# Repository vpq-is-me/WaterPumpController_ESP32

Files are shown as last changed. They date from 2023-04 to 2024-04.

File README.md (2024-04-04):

# Water pump controller.

This controller intended for control submersible pump installed in water well. It turn on pump when pressure in hydraulic accumulator (HA) dropped to lower pressure P1 and switch off when pressure rich high predefined pressure P2. Pressure measured by pressure transducer with range 0-6bar and output 4-20mA. 
For diagnostic reason there is water flow counter with pulse output - 1 pulse per 10litres (dry contact). 

In series with this controller installed external simple pressure switch (optional). It's aim is protection of system in case of controller failure. For normal work this pressure switch must tunned with upper disconnection pressure above controller's upper pressure P2. For exmple if controller's switch off pressure is 3.2 bar external pressure switch can be 3.5 bar. In case of controller failure or for test reason Bypass switch can be operated. It shorted controlle's output switch and in this case external pressure switch mantaine HA pressure.

This controller connected to Bluetooth MESH net and broadcast internal data, e.i. to [home_automation_server](https://github.com/vpq-is-me/home_auto_nodejs.git) (running on Raspberry Pi) for diagnostic and send message to Telegram bot in case of alarm.
 
Via Bluetooth MESH controller receive state of [Sewage Treatment System (STS)](https://github.com/vpq-is-me/SepticProtectionESP32.git) - (automomous canalization) and in case of STS overfill controller stops water feeding.

Also it stops water feeding in case of some failure:
   - dropped air pressure in Hydraulic Accumulator (air leak)
   - pump failure
   - pump capacity dropping 

### Entire system overview

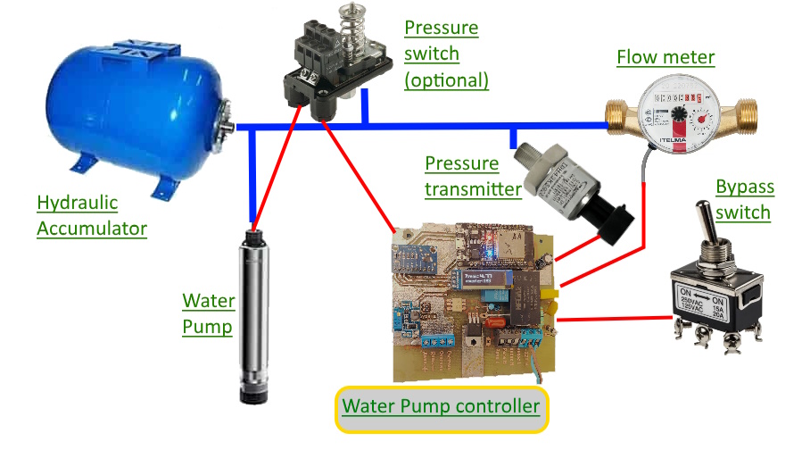
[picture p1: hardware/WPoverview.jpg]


### Controller circuit diagram
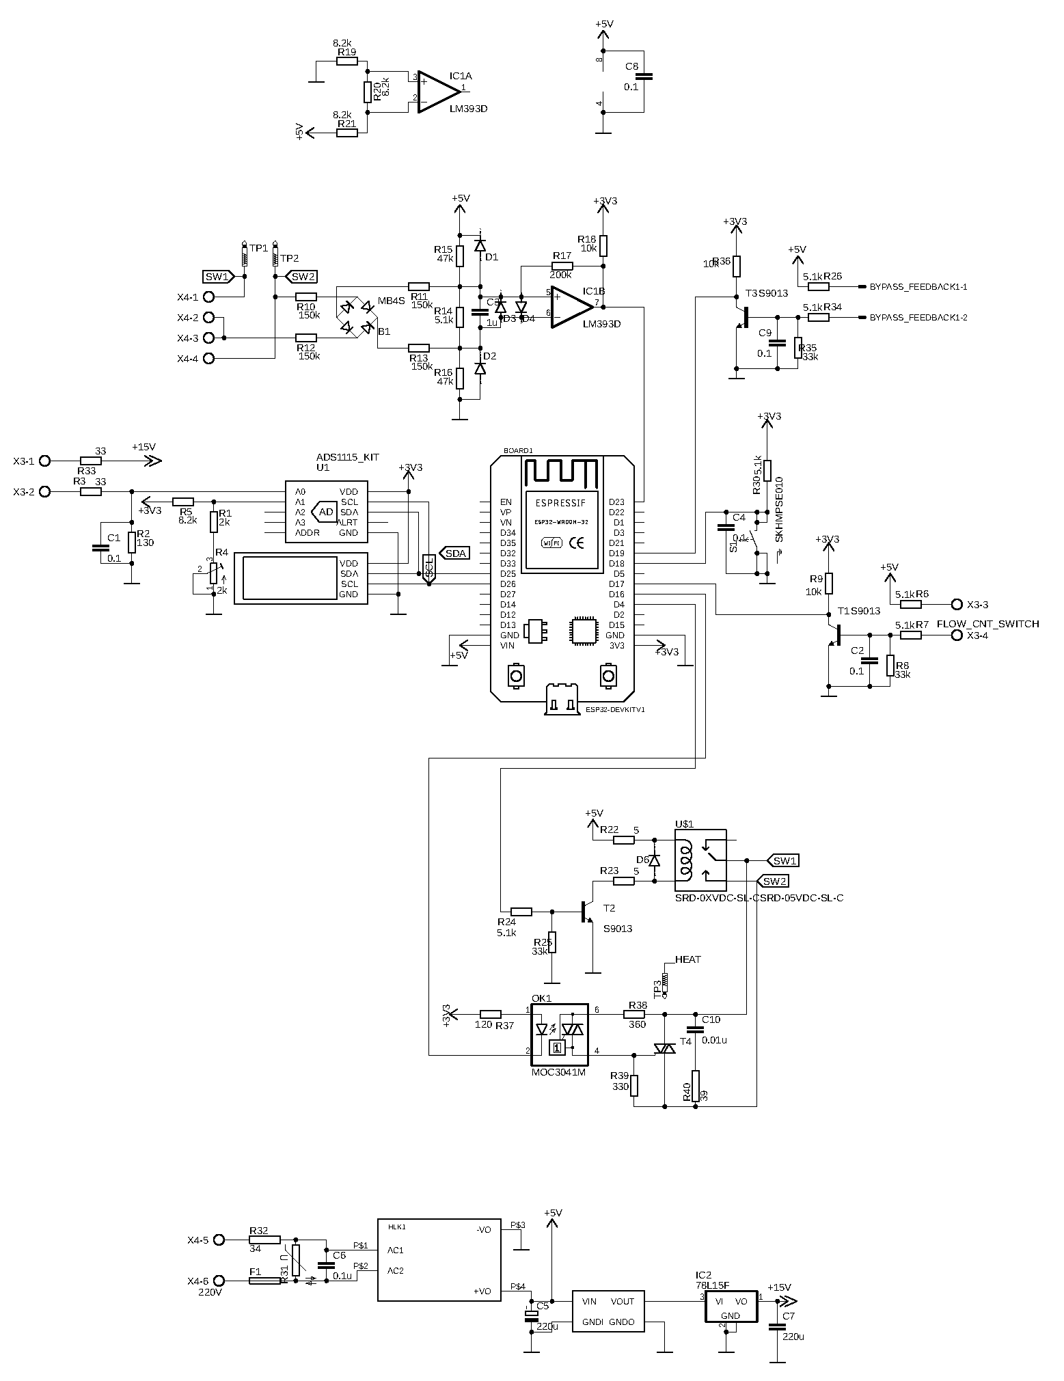
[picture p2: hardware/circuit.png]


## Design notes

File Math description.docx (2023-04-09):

(*)

- давление воздуха в гидроаккумуляторе (ГА) без воды

# - полный объем ГА

- нижнее и верхнее давления срабатывания прессостата

- объем воздуха в гидроаккумуляторе при заполнении водой до нижнего и верхнего давления соответственно

# - рабочий объем воды в ГА

# Внимание! Все давления в расчетах являются абсолютными!

Расчет объема ГА производится в моменты счетных импульсов водяного счетчика. Обычно цена деления импульсов равна 10л.

-объем воздуха в моменты времени импульсов от счетчика воды

- добавочный объем воды, залитый в ГА при повышении давления от

- давление воды (и воздуха) в текущий и предыдущий моменты импульсов от счетчика

# Значит

Отсюда расчетный объем воздуха в ГА при минимальном давлении воды, исходя из измеренных давлений , и объемов воды

(2)

# Далее принимая во внимание

Подставляем сюда (2)

Окончательно полезный объем воды в ГА:

(3)

- объем воды, залитый (+) или слитый (-) в/из ГА между текущим и предыдущим счетными импульсами. Рассчитывается исходя из потребленного объема между импульсами, т.е. 10 литров и закачанной насосом воды, которая равна произведению производительности насоса на время его работы.

(4)

Из выражения (1) аналогично для других случайных пар давлений, исходя из паспортных значений объем воды слитый/залитый в ГА можно рассчитать по разнице объема воздуха (!) в танке:

(5)

Выражение 3 совместно с 4 используем для расчета полезного объема ГА по измеренным значениям. Выражение 5 используем при расчетах производительности насоса, как описано далее. За несколько импульсов счетчика воды измеряем время работы насоса. Объем потребленной воды измерен счетчиком, добавляем (отнимаем) к нему объем запасенной (слитой) воды в ГА. Производительность, очевидно, - объем на время.

Внимание! Если давления близки друг к другу, особенно если разница равна нулю, в таком случае рассчитать объем ГА по (3) нельзя (деление на ноль)!

В программе необходимо переводить относительные давления в абсолютные. Для величин в барах добавляем 1.

Всё это хрень! При быстром изменении давления процесс адиабатный, а не изотермический!!! Смотри формулы и использование в файле лога и модели на питоне!!!

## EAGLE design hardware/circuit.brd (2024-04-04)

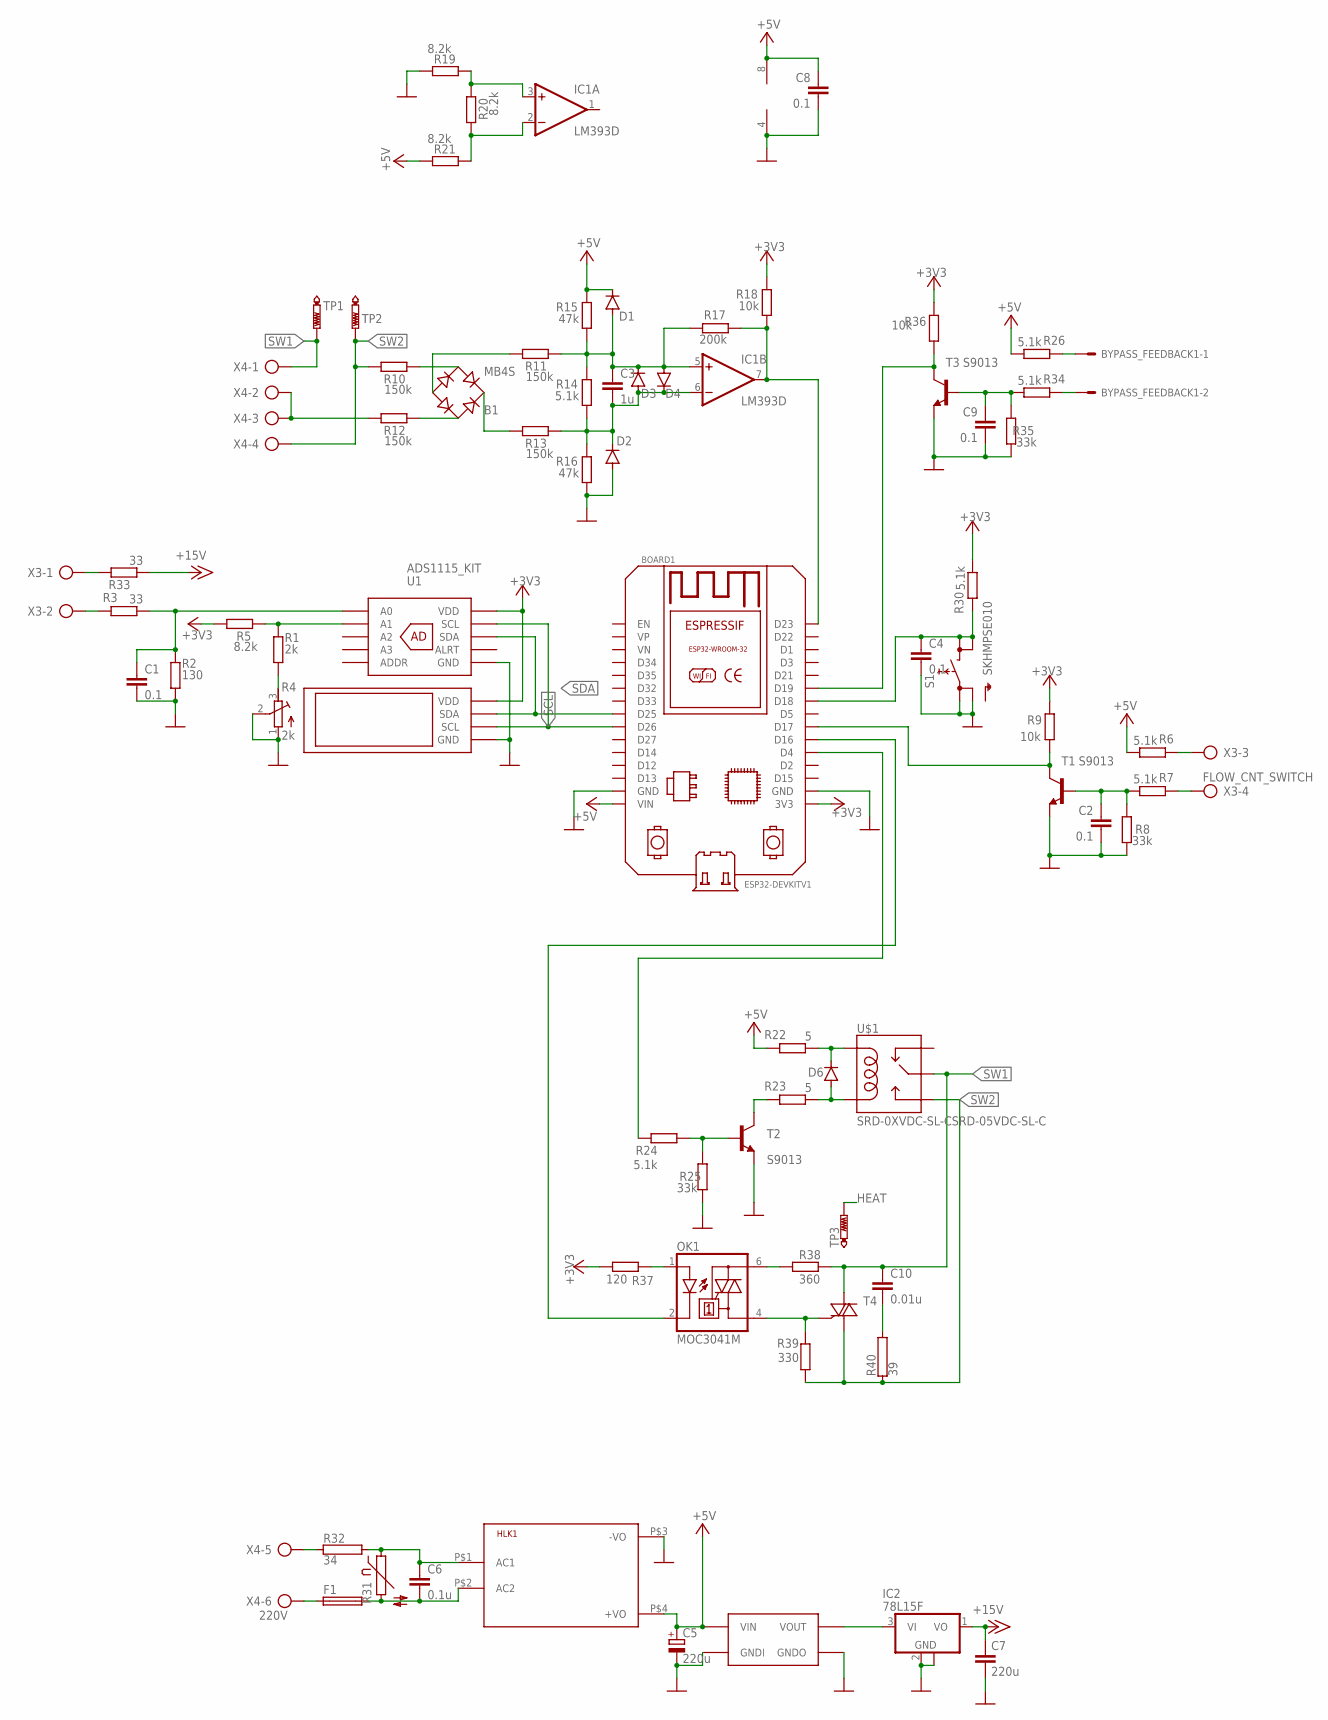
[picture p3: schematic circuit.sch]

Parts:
B1: MB4S; SOIC-4
BOARD1: ESP32DEVKITV1; ESP32-DEVKITV1
BYPASS_FEEDBACK1: C-GRID-02-70543; 70543-02
C1, C2, C4, C8, C9: 0.1; C1206
C3: 1u; C1206
C5: 220u; E3,5-8
C6: 0.1u; C10B5
C7: 220u; C1210K
C10: 0.01u; C10B5
D1, D2, D3, D4, D6: CGRM4001-G; SOD-123_MINI-SMA
DC1: HW-668_DC_DC_STEPUP
F1: FUSE19560; 19560
HLK1: HLK-PM013W; HLK-PM01
IC1: LM393D; SO08
IC2: 78L15F; SOT89
OK1: MOC3041M; DIL06
R1: 2k; R1206
R2: 130; R1206
R3, R33: 33; R1206
R4: 2k; RTRIM3202
R5, R19, R20, R21: 8.2k; R1206
R6, R7, R14, R24, R26, R30, R34: 5.1k; R1206
R8, R25, R35: 33k; R1206
R9, R18, R36: 10k; R1206
R10, R11, R12, R13: 150k; R1206
R15, R16: 47k; R1206
R17: 200k; R1206
R22, R23: 5; R1206
R31: S10K510
R32: 34; CA0001
R37: 120; R1206
R38: 360; R1206
R39: 330; R1206
R40: 39; CA0001
S1: SKHMPSE010; SKHMPXE010
T1, T2, T3: S9013; SOT23-BEC
T4: BT136; TO220AB
TP1, TP2: PTR1PAD1-20Y; P1-20Y
TP3: PTR1B1,27; B1,27
U1: ADS1115_KIT
U2: SSD1306_OLED
U$1: SRD-0XVDC-SL-CSRD-05VDC-SL-C; SRD-0XVDC-SL-C
X3: FLOW_CNT_SWITCH; AK300/4
X4: 220V; AK300/6

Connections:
+3V3: BOARD1.3V3, R5.2, R9.1, R18.1, R30.1, R36.1, R37.1, U1.P$1 (VDD), U2.P$3 (VDD)
+5V: BOARD1.VIN, C5.+, C8.1, D1.C, DC1.P$1 (VIN), HLK1.P$4 (+VO), IC1.8 (V+), R6.1, R15.1, R21.1, R22.2, R26.1
+15V: C7.1, IC2.1 (VO), R33.1
FLOW_SW: BOARD1.D17, R9.2, T1.C
GND: BOARD1.GND, BOARD1.GND@1 (GND), C1.2, C2.2, C4.2, C5.-, C7.2, C8.2, C9.2, D2.A, DC1.P$2 (GNDI), DC1.P$3 (GNDO), HLK1.P$3 (-VO), IC1.4 (V-), IC2.2 (GND), IC2.2@1 (GND), R2.1, R4.1 (A), R4.2 (S), R8.2, R16.2, R19.1, R25.2, R35.2, S1.1 (1.1), S1.2 (1.2), T1.E, T2.E, T3.E, U1.P$2 (GND), U2.P$4 (GND)
HEAT: TP3.TP
unnamed: C9.1, R34.1, R35.1, T3.B
unnamed: BYPASS_FEEDBACK1.1, R26.2
unnamed: C1.1, R2.2, R3.1, U1.P$7 (A0)
unnamed: R1.2, R5.1, U1.P$8 (A1)
unnamed: R1.1, R4.3 (E)
unnamed: C2.1, R7.1, R8.1, T1.B
unnamed: R33.2, X3.1
unnamed: B1.+, R13.2
unnamed: C3.2, D2.C, D3.A, D4.C, IC1.6 (-IN), R13.1, R14.2, R16.1
unnamed: C3.1, D1.A, D3.C, D4.A, IC1.5 (+IN), R11.1, R14.1, R15.2, R17.1
unnamed: B1.-, R11.2
unnamed: R32.1, X4.5
unnamed: B1.~2 (AC2), R10.1
unnamed: B1.~1 (AC1), R12.1
unnamed: R23.2, T2.C
unnamed: IC1.3 (+IN), R19.2, R20.1
unnamed: IC1.2 (-IN), R20.2, R21.2
unnamed: D6.C, R22.1, U$1.COIL1
unnamed: F1.1, X4.6
unnamed: R3.2, X3.2
unnamed: BYPASS_FEEDBACK1.2, R34.2
unnamed: R24.1, R25.1, T2.B
unnamed: R12.2, X4.2, X4.3
unnamed: R6.2, X3.3
unnamed: C6.1, HLK1.P$1 (AC1), R31.1, R32.2
unnamed: C6.2, F1.2, HLK1.P$2 (AC2), R31.2
unnamed: D6.A, R23.1, U$1.COIL0
unnamed: DC1.P$4 (VOUT), IC2.3 (VI)
unnamed: R7.2, X3.4
unnamed: BOARD1.D19, R36.2, T3.C
unnamed: BOARD1.D16, OK1.2 (C)
unnamed: OK1.1 (A), R37.2
unnamed: OK1.6 (A2), R38.1
unnamed: OK1.4 (A1), R39.2, T4.3 (G)
unnamed: C10.2, R40.2
PP_ON: BOARD1.D23, IC1.7 (OUT), R17.2, R18.2
RST_ALR: BOARD1.D18, C4.1, R30.2, S1.3 (2.1), S1.4 (2.2)
SCL: BOARD1.D26, U1.P$3 (SCL), U2.P$2 (SCL)
SDA: BOARD1.D25, U1.P$4 (SDA), U2.P$1 (SDA)
SSRELAY_ON: BOARD1.D4, R24.2
SW1: C10.1, R38.2, T4.2 (A2), TP1.TP, U$1.SWCOMMON, X4.1
SW2: R10.2, R39.1, R40.1, T4.1 (A1), TP2.TP, U$1.SWOPEN, X4.4

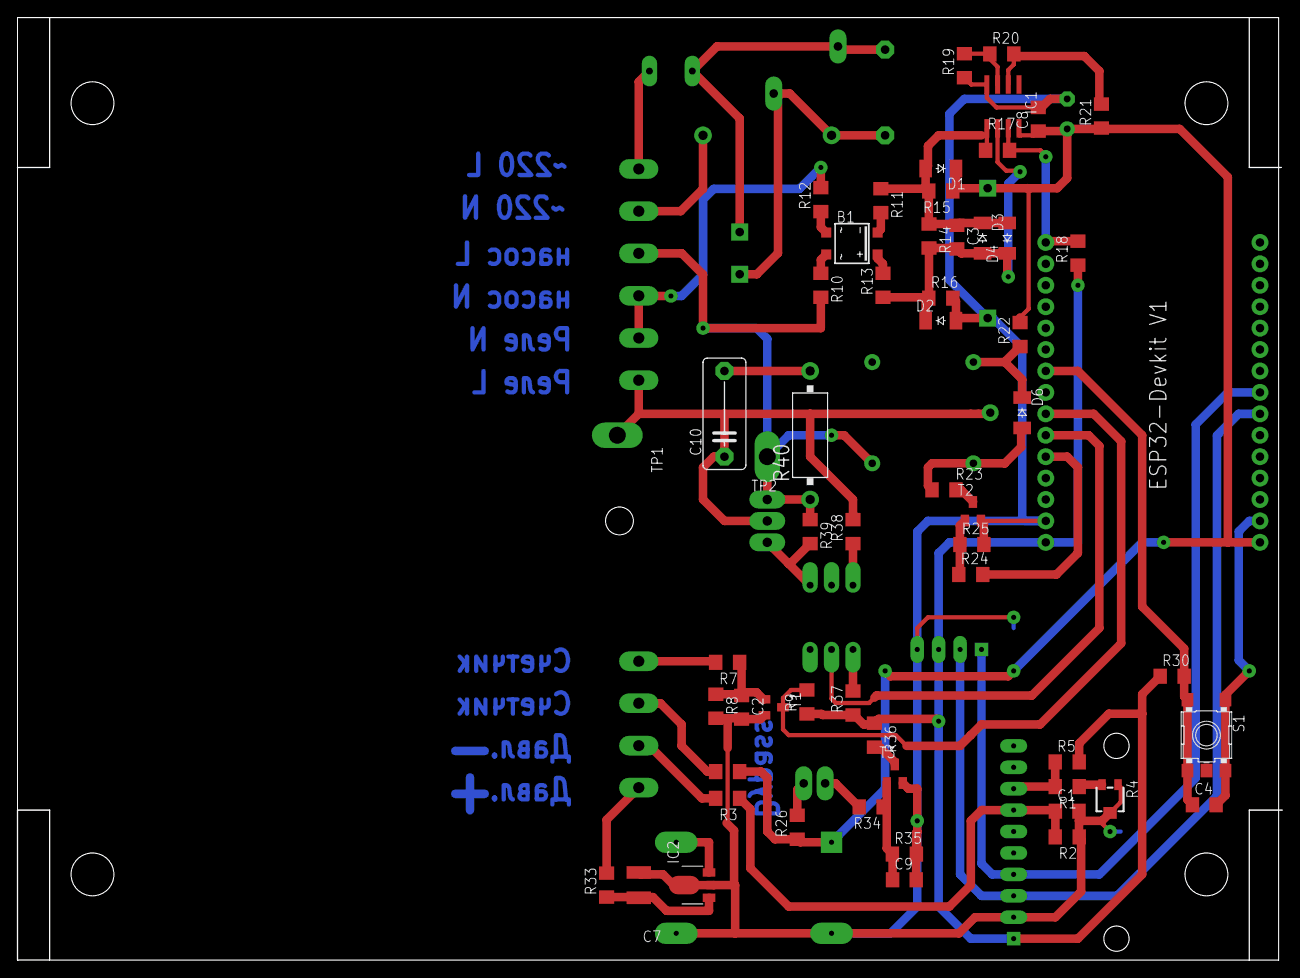
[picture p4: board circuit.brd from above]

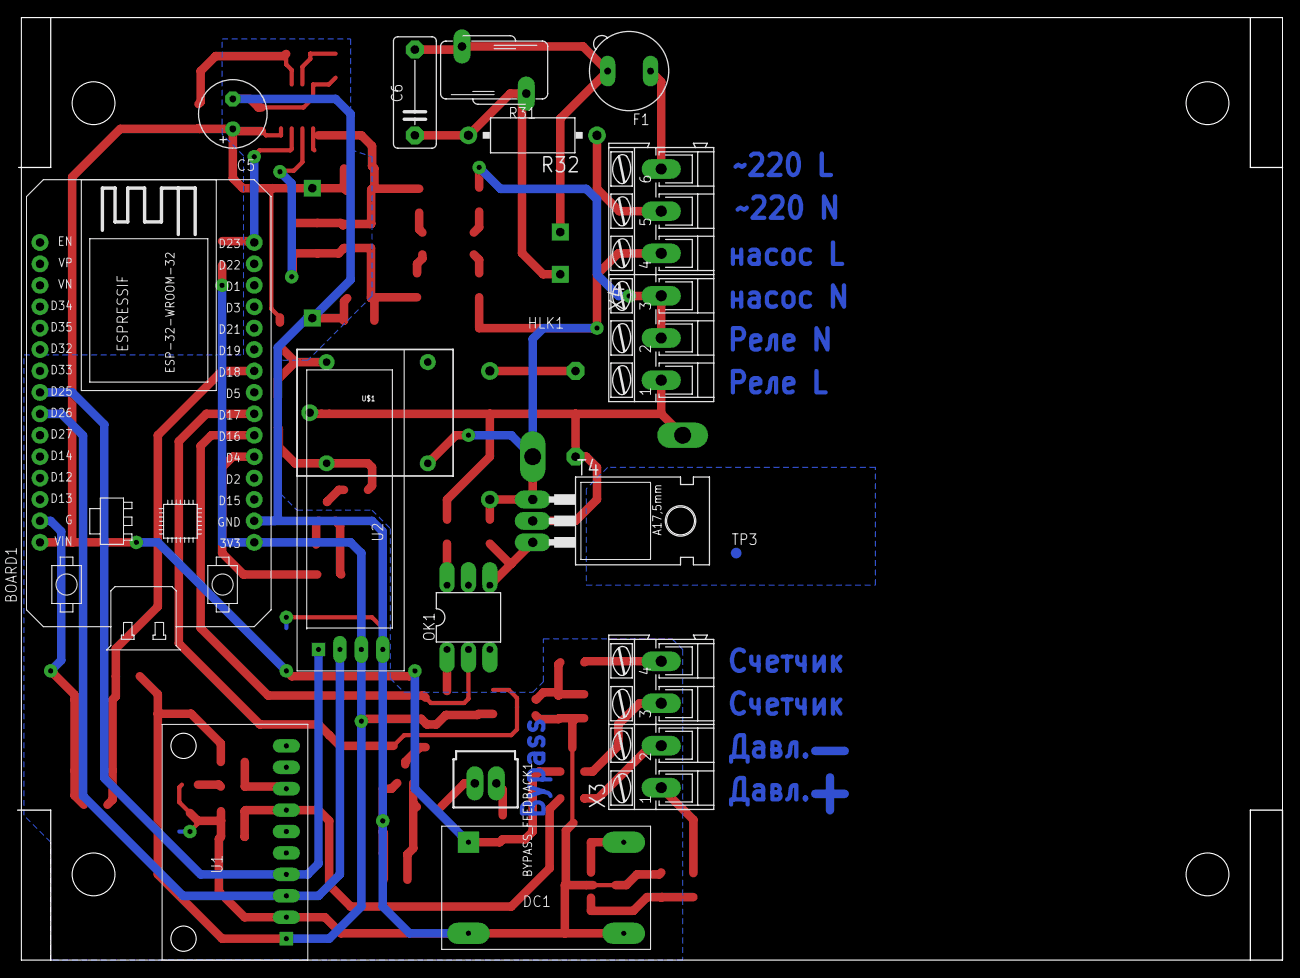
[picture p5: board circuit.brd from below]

Board: 2 copper layers, 149.5 x 111.8 mm, 74 parts (17 on the bottom side), 47 nets.

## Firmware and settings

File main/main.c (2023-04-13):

/* main.c - Application main entry point */

/*
 * Copyright (c) 2017 Intel Corporation
 * Additional Copyright (c) 2018 Espressif Systems (Shanghai) PTE LTD
 *
 * SPDX-License-Identifier: Apache-2.0
 */

#include <stdio.h>
#include <string.h>

#include "ble_mesh_example_init.h"
#include "board.h"
#include "esp_ble_mesh_common_api.h"
#include "esp_ble_mesh_config_model_api.h"
#include "esp_ble_mesh_defs.h"
#include "esp_ble_mesh_local_data_operation_api.h"
#include "esp_ble_mesh_networking_api.h"
#include "esp_ble_mesh_provisioning_api.h"
#include "esp_bt.h"
#include "esp_log.h"
#include "nvs_flash.h"
#include "loop.h"
#include "main.h"



//NOTE proxy server name that will be shown in phone or PC new device list is located in
//C:/esp/esp-idf/components/bt/esp_ble_mesh/mesh_core/proxy_server.c in 
//strncpy(device_name, "ESP-BLE-MESH", DEVICE_NAME_SIZE);
//but better use 
// int bt_mesh_set_device_name(const char*name) 

#define TAG "EXAMPLE"

#define MAX_MSG_LENGTH 8
#define PUBLISH_RETRANSMIT_COUNT 0
#define PUBLISH_RETRANSMIT_PERIOD 50 /* not use less 50 otherwise it will turn to negative value in ESP_BLE_MESH_PUBLISH_TRANSMIT macro*/

#define CREATE_GROUP_ADDR(add) ((uint16_t)0xc000 | add)
#define GROUP_SEPTIC CREATE_GROUP_ADDR(10)
#define GROUP_DOORBELL CREATE_GROUP_ADDR(11)
#define GROUP_WATERPUMP CREATE_GROUP_ADDR(12)

//#define ESP_BLE_MESH_VND_MODEL_ID_CLIENT 0x0000
#define WATER_PUMP_MODEL_ID_SERVER 0x0001
#define SEPTIC_MODEL_ID_SERVER    0x0002

static uint8_t dev_uuid[ESP_BLE_MESH_OCTET16_LEN] = {0x32, 0x10};
static esp_ble_mesh_cfg_srv_t config_server = {
    .relay = ESP_BLE_MESH_RELAY_ENABLED,
    .beacon = ESP_BLE_MESH_BEACON_ENABLED,
#if defined(CONFIG_BLE_MESH_FRIEND)
    .friend_state = ESP_BLE_MESH_FRIEND_ENABLED,
#else
    .friend_state = ESP_BLE_MESH_FRIEND_NOT_SUPPORTED,
#endif
#if defined(CONFIG_BLE_MESH_GATT_PROXY_SERVER)
    .gatt_proxy = ESP_BLE_MESH_GATT_PROXY_ENABLED,
#else
    .gatt_proxy = ESP_BLE_MESH_GATT_PROXY_NOT_SUPPORTED,
#endif
    .default_ttl = 7,
    /* 3 transmissions with 20ms interval */
    .net_transmit = ESP_BLE_MESH_TRANSMIT(3, 50),
    .relay_retransmit = ESP_BLE_MESH_TRANSMIT(3, 50),
    //vpq: Best result 4 retransmition with 50ms interval. It can be changed from android application 
};

static esp_ble_mesh_model_t root_models[] = {
    ESP_BLE_MESH_MODEL_CFG_SRV(&config_server),
};

static esp_ble_mesh_model_op_t vnd_op[] = {
    ESP_BLE_MESH_MODEL_OP(WATER_PUMP_OP_SET_PARAM, 5),
    ESP_BLE_MESH_MODEL_OP(WATER_PUMP_OP_GET_PARAM, 1),
    ESP_BLE_MESH_MODEL_OP(WATER_PUMP_OP_STATUS_PARAM, 5), 

    ESP_BLE_MESH_MODEL_OP(WATER_PUMP_OP_STATUS_COUNTER, 4),
    ESP_BLE_MESH_MODEL_OP(WATER_PUMP_OP_STATUS_CAPACITY, 4),
    ESP_BLE_MESH_MODEL_OP(WATER_PUMP_OP_STATUS_TK_VOL, 4),
    ESP_BLE_MESH_MODEL_OP(WATER_PUMP_OP_STATUS_ALARM, 4),
    ESP_BLE_MESH_MODEL_OP(WATER_PUMP_OP_STATUS_PP_TIMEOUTS, 8),
    ESP_BLE_MESH_MODEL_OP(WATER_PUMP_OP_STATUS_CAP_AVG, 4),
    ESP_BLE_MESH_MODEL_OP_END,
};

static const esp_ble_mesh_client_op_pair_t septic_vnd_op_pair[] = {
    { SEPTIC_OP_GET, SEPTIC_OP_ALARM_STATUS },
    { SEPTIC_OP_GET, SEPTIC_OP_PEND_ALARM_STATUS },
};

static esp_ble_mesh_client_t septic_client = {
    .op_pair_size = ARRAY_SIZE(septic_vnd_op_pair),
    .op_pair = septic_vnd_op_pair,
};
static esp_ble_mesh_model_op_t vnd_septic_op[] = {
//    ESP_BLE_MESH_MODEL_OP(SEPTIC_OP_SET, 2),
    ESP_BLE_MESH_MODEL_OP(SEPTIC_OP_GET, 1),
    ESP_BLE_MESH_MODEL_OP(SEPTIC_OP_ALARM_STATUS, 1),
    ESP_BLE_MESH_MODEL_OP(SEPTIC_OP_PEND_ALARM_STATUS, 1),
    ESP_BLE_MESH_MODEL_OP_END,
};



ESP_BLE_MESH_MODEL_PUB_DEFINE(vnd_pub, (3 + MAX_MSG_LENGTH), ROLE_NODE);  // MAX_MSG_LENGTH + length(op_code)
static esp_ble_mesh_model_t vnd_models[] = {
    ESP_BLE_MESH_VENDOR_MODEL(CID_ESP, WATER_PUMP_MODEL_ID_SERVER,
                              vnd_op, &vnd_pub, NULL),
    ESP_BLE_MESH_VENDOR_MODEL(CID_ESP, SEPTIC_MODEL_ID_SERVER,
                              vnd_septic_op, &vnd_pub, &septic_client),
};

// Call this function after provision completed!Even after bind key
void set_publish(void) {
    vnd_pub.retransmit = ESP_BLE_MESH_PUBLISH_TRANSMIT(PUBLISH_RETRANSMIT_COUNT, PUBLISH_RETRANSMIT_PERIOD);
    vnd_pub.ttl = 0x07;
    vnd_pub.publish_addr = GROUP_WATERPUMP;
//    Note. If you subscribed one time it will be remembered in storage, so explicitly unsubscribe!
    // esp_ble_mesh_model_unsubscribe_group_addr(vnd_models[0].element->element_addr,
    //                                           vnd_models[0].vnd.company_id,
    //                                           vnd_models[0].vnd.model_id,
    //                                           GROUP_SEPTIC);
    esp_ble_mesh_model_subscribe_group_addr(vnd_models[1].element->element_addr,
                                            vnd_models[1].vnd.company_id,
                                            vnd_models[1].vnd.model_id,
                                            GROUP_SEPTIC);
    //if you subscribe on your publish address you will receive you own group messages in ESP_BLE_MESH_MODEL_OPERATION_EVT
    //Or filter this messages or don't subscribe
    //Note. If you subscribed one time it will be remembered in storage, so explicitly unsubscribe!
    // esp_ble_mesh_model_unsubscribe_group_addr(vnd_models[0].element->element_addr,
    //                                           vnd_models[0].vnd.company_id,
    //                                           vnd_models[0].vnd.model_id,
    //                                           GROUP_WATERPUMP);
    // esp_ble_mesh_model_subscribe_group_addr(vnd_models[0].element->element_addr,//!!!! delete. may be receive only by node address
    //                                         vnd_models[0].vnd.company_id,
    //                                         vnd_models[0].vnd.model_id,
    //                                         GROUP_WATERPUMP);

}

//*****************************************************************************************************

static esp_ble_mesh_elem_t elements[] = {
        ESP_BLE_MESH_ELEMENT(0, root_models, vnd_models),
};

static esp_ble_mesh_comp_t composition = {
    .cid = CID_ESP,
    .elements = elements,
    .element_count = ARRAY_SIZE(elements),
};

static esp_ble_mesh_prov_t provision = {
    .uuid = dev_uuid,
};

static void prov_complete(uint16_t net_idx, uint16_t addr, uint8_t flags, uint32_t iv_index) {
    ESP_LOGI(TAG, "net_idx 0x%03x, addr 0x%04x", net_idx, addr);
    LED_toggle();
}

static void ble_mesh_provisioning_cb(esp_ble_mesh_prov_cb_event_t event,
                                             esp_ble_mesh_prov_cb_param_t *param) {
    switch (event) {
        case ESP_BLE_MESH_PROV_REGISTER_COMP_EVT:
            ESP_LOGI(TAG, "ESP_BLE_MESH_PROV_REGISTER_COMP_EVT, err_code %d", param->prov_register_comp.err_code);
            break;
        case ESP_BLE_MESH_NODE_PROV_ENABLE_COMP_EVT:
            ESP_LOGI(TAG, "ESP_BLE_MESH_NODE_PROV_ENABLE_COMP_EVT, err_code %d", param->node_prov_enable_comp.err_code);
            break;
        case ESP_BLE_MESH_NODE_PROV_LINK_OPEN_EVT:
            ESP_LOGI(TAG, "ESP_BLE_MESH_NODE_PROV_LINK_OPEN_EVT, bearer %s",
                     param->node_prov_link_open.bearer == ESP_BLE_MESH_PROV_ADV ? "PB-ADV" : "PB-GATT");
            break;
        case ESP_BLE_MESH_NODE_PROV_LINK_CLOSE_EVT:
            ESP_LOGI(TAG, "ESP_BLE_MESH_NODE_PROV_LINK_CLOSE_EVT, bearer %s",
                     param->node_prov_link_close.bearer == ESP_BLE_MESH_PROV_ADV ? "PB-ADV" : "PB-GATT");
            break;
        case ESP_BLE_MESH_NODE_PROV_COMPLETE_EVT:
            ESP_LOGI(TAG, "ESP_BLE_MESH_NODE_PROV_COMPLETE_EVT");
            prov_complete(param->node_prov_complete.net_idx, param->node_prov_complete.addr,
                          param->node_prov_complete.flags, param->node_prov_complete.iv_index);
            break;
        case ESP_BLE_MESH_NODE_PROV_RESET_EVT:
            ESP_LOGI(TAG, "ESP_BLE_MESH_NODE_PROV_RESET_EVT");
            break;
        case ESP_BLE_MESH_NODE_SET_UNPROV_DEV_NAME_COMP_EVT:
            ESP_LOGI(TAG, "ESP_BLE_MESH_NODE_SET_UNPROV_DEV_NAME_COMP_EVT, err_code %d", param->node_set_unprov_dev_name_comp.err_code);
            break;
        default:
            break;
    }
}

static void ble_mesh_config_server_cb(esp_ble_mesh_cfg_server_cb_event_t event,
                                              esp_ble_mesh_cfg_server_cb_param_t *param) {
    if (event == ESP_BLE_MESH_CFG_SERVER_STATE_CHANGE_EVT) {
        switch (param->ctx.recv_op) {
            case ESP_BLE_MESH_MODEL_OP_APP_KEY_ADD:
                ESP_LOGI(TAG, "ESP_BLE_MESH_MODEL_OP_APP_KEY_ADD");
                ESP_LOGI(TAG, "net_idx 0x%04x, app_idx 0x%04x",
                         param->value.state_change.appkey_add.net_idx,
                         param->value.state_change.appkey_add.app_idx);
                ESP_LOG_BUFFER_HEX("AppKey", param->value.state_change.appkey_add.app_key, 16);
                break;
            case ESP_BLE_MESH_MODEL_OP_MODEL_APP_BIND:
                ESP_LOGI(TAG, "ESP_BLE_MESH_MODEL_OP_MODEL_APP_BIND");
                ESP_LOGI(TAG, "elem_addr 0x%04x, app_idx 0x%04x, cid 0x%04x, mod_id 0x%04x",
                         param->value.state_change.mod_app_bind.element_addr,
                         param->value.state_change.mod_app_bind.app_idx,
                         param->value.state_change.mod_app_bind.company_id,
                         param->value.state_change.mod_app_bind.model_id);
                set_publish();
                break;
            // case ESP_BLE_MESH_MODEL_OP_RELAY_SET:
            //     ESP_LOGI(TAG, "relay %d, relay retrans 0x%02x",
            //              param->value.state_change.relay_set.relay,
            //              param->value.state_change.relay_set.relay_retransmit);
            //     break;
            default:
                break;
        }
    }
}

static void ble_mesh_custom_model_cb(esp_ble_mesh_model_cb_event_t event,
                                             esp_ble_mesh_model_cb_param_t *param) {
    switch (event) {
        case ESP_BLE_MESH_MODEL_OPERATION_EVT:
            ESP_LOGI(TAG, "receive message from peer with rmt addr 0x%04x, dst_addr 0x%04x",
                            param->model_operation.ctx->addr,param->model_operation.ctx->recv_dst);
            if(param->model_operation.opcode==WATER_PUMP_OP_SET_PARAM) {
                uint8_t id;
                int32_t val;
                set_get_message_st *cmd=(set_get_message_st*)param->model_operation.msg;
                set_get_message_st answer;
                id=cmd->id;
                val=cmd->val;
                answer.val=WPSetParameter(id,val);
                answer.id=id;
                ESP_LOGI(TAG, "SET message-> param ID=%d, answer=0x%04x",*param->model_operation.msg,answer.val);
                esp_err_t err = esp_ble_mesh_server_model_send_msg(&vnd_models[0],
                                        param->model_operation.ctx, WATER_PUMP_OP_STATUS_PARAM,
                                        sizeof(answer), (uint8_t *)&answer);
                if (err) ESP_LOGE(TAG, "Failed to send message 0x%06x", WATER_PUMP_OP_STATUS_PARAM);
            }else{//only WATER_PUMP_OP_GET_PARAM posible
                uint8_t id;
                set_get_message_st answer;
                id=*param->model_operation.msg;
                answer.val=WPGetParameter(id);
                answer.id=id;
                ESP_LOGI(TAG, "GET message-> param ID=%d, answer=0x%04x",*param->model_operation.msg,answer.val);
                esp_err_t err = esp_ble_mesh_server_model_send_msg(&vnd_models[0],
                                        param->model_operation.ctx, WATER_PUMP_OP_STATUS_PARAM,
                                        sizeof(answer), (uint8_t *)&answer);
                if (err) ESP_LOGE(TAG, "Failed to send message 0x%06x", WATER_PUMP_OP_STATUS_PARAM);
            }
            break;
        case ESP_BLE_MESH_MODEL_SEND_COMP_EVT:
            if (param->model_send_comp.err_code) {
                ESP_LOGE(TAG, "Failed to send message 0x%06x", param->model_send_comp.opcode);
                break;
            }
            ESP_LOGI(TAG, "Send 0x%06x", param->model_send_comp.opcode);
            break;
        case ESP_BLE_MESH_MODEL_PUBLISH_COMP_EVT:
            LED_toggle();
//            ESP_LOGI(TAG, "Complete publish message with result err=%d", param->model_publish_comp.err_code);
            break;
        case ESP_BLE_MESH_CLIENT_MODEL_RECV_PUBLISH_MSG_EVT:
            ESP_LOGI(TAG,"We receive publish message length=%d",param->client_recv_publish_msg.length);
            ESP_LOGI(TAG,"opcode: 0x%06x; src_addr: 0x%04x, dst_addr: 0x%04x",param->client_recv_publish_msg.opcode,
                                                                              param->client_recv_publish_msg.ctx->addr,
                                                                              param->client_recv_publish_msg.ctx->recv_dst);
            if(param->client_recv_publish_msg.ctx->recv_dst==GROUP_SEPTIC){
                if(param->client_recv_publish_msg.opcode==SEPTIC_OP_PEND_ALARM_STATUS){
                    uint8_t msg_data=*param->client_recv_publish_msg.msg;
                    WPSetSepticState(msg_data);
                }
            }
            break;
        default:
            ESP_LOGI(TAG, "Unproccessed event in model CB event: %d", event);
            break;
    }
}
void vendor_publish_message(uint32_t op_code, uint8_t*data, uint16_t length) {
    esp_ble_mesh_model_publish(&vnd_models[0], op_code, length, data, ROLE_NODE);
}
static esp_err_t ble_mesh_init(void) {
    esp_err_t err;

    esp_ble_mesh_register_prov_callback(ble_mesh_provisioning_cb);
    esp_ble_mesh_register_config_server_callback(ble_mesh_config_server_cb);
    esp_ble_mesh_register_custom_model_callback(ble_mesh_custom_model_cb);

    err = esp_ble_mesh_init(&provision, &composition);
    if (err != ESP_OK) {
        ESP_LOGE(TAG, "Failed to initialize mesh stack");
        return err;
    }

    err = esp_ble_mesh_client_model_init(&vnd_models[1]);
    if (err) {
        ESP_LOGE(TAG, "Failed to initialize vendor client");
        return err;
    }

    err = esp_ble_mesh_node_prov_enable(ESP_BLE_MESH_PROV_ADV | ESP_BLE_MESH_PROV_GATT);
    if (err != ESP_OK) {
        ESP_LOGE(TAG, "Failed to enable mesh node");
        return err;
    }

    bt_mesh_set_device_name("Home/Water PP");
    esp_ble_tx_power_set(ESP_BLE_PWR_TYPE_DEFAULT,ESP_PWR_LVL_P9);
    esp_ble_tx_power_set(ESP_BLE_PWR_TYPE_ADV,ESP_PWR_LVL_P9);
    esp_ble_tx_power_set(ESP_BLE_PWR_TYPE_SCAN,ESP_PWR_LVL_P9);
    ESP_LOGI(TAG, "BLE Mesh Node initialized");
    set_publish();
    return ESP_OK;
}

void app_main(void) {
    esp_err_t err;

    ESP_LOGI(TAG, "Initializing...");

    err = nvs_flash_init();
    if (err == ESP_ERR_NVS_NO_FREE_PAGES) {
        ESP_ERROR_CHECK(nvs_flash_erase());
        err = nvs_flash_init();
    }
    ESP_ERROR_CHECK(err);

    board_init();
    err = bluetooth_init();
    if (err) {
        ESP_LOGE(TAG, "esp32_bluetooth_init failed (err %d)", err);
        return;
    }

    ble_mesh_get_dev_uuid(dev_uuid);

    /* Initialize the Bluetooth Mesh Subsystem */
    err = ble_mesh_init();
    if (err) {
        ESP_LOGE(TAG, "Bluetooth mesh init failed (err %d)", err);
    }
    xTaskCreate(loop_task,"main_loop_task",LOOP_STACK_SIZE,NULL,10,NULL);
 }
//bt_mesh_net_relay

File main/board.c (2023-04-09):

/* board.c - Board-specific hooks */

/*
 * Copyright (c) 2017 Intel Corporation
 * Additional Copyright (c) 2018 Espressif Systems (Shanghai) PTE LTD
 *
 * SPDX-License-Identifier: Apache-2.0
 */

#include <stdio.h>
#include "driver/gpio.h"
#include "esp_log.h"
#include "board.h"
#include "loop.h"
#include "display_adc.h"
#include <math.h>
// #include "iot_button.h"



#define TAG "BOARD"
#define TIMER_GRANUL_MS 10
//**********************************************************************************
void LED_operation(uint8_t onoff){
    gpio_set_level(LED_B, onoff);
}
void LED_toggle(){
    gpio_set_level(LED_B,!gpio_get_level(LED_B));
}

static void board_led_init(void)
{
    gpio_reset_pin(LED_B);
    gpio_set_direction(LED_B, GPIO_MODE_OUTPUT);
    gpio_set_level(LED_B, LED_OFF);
}
void board_init(void) {
    board_led_init();
    gpio_reset_pin(BOARD_BUTTON_PIN);
    gpio_set_direction(BOARD_BUTTON_PIN, GPIO_MODE_INPUT);
    // board_button_init();
}

//****************************************
// #define BUTTON_IO_NUM 0
// #define BUTTON_ACTIVE_LEVEL 0

// //void vendor_publish_message(void);

// static void button_tap_cb(void *arg) {
//     //    print_vnd_data();
//  //   vendor_publish_message();
// }

// static void board_button_init(void) {
//     button_handle_t btn_handle = iot_button_create(BUTTON_IO_NUM, BUTTON_ACTIVE_LEVEL);
//     if (btn_handle) {
//         iot_button_set_evt_cb(btn_handle, BUTTON_CB_RELEASE, button_tap_cb, "RELEASE");
//     }
// }
static uint8_t button_state=0xff;
static volatile uint8_t button_was_pressed=0;
uint8_t IsButtonPressed(void){
    uint8_t res=button_was_pressed;
    if(res){
        button_was_pressed=0;
    }
    return res;
}
//****************************************
typedef struct{
    uint8_t counter_in_states; //shift register of state of flow-counter input 
    uint8_t pump_power_in_states; //shift register of state of pump power input 
    uint32_t pump_on_timer;//pump working time from pump start, for long run check,in timer granuality 
    uint32_t pump_off_timer;//pump not working time from last stop, for frequent restart check,in timer granuality
    uint8_t pump_run_fg;
    TickType_t pump_on_acc;//accumulated timer of working time from last flow-counter pulse
    TickType_t pump_last_start_2acc;//time of last start of pump, used for accumulation of working time from one flowcounter pulse to another. It is reseted at every pulse
    TickType_t pump_last_start_pure;//time of last start of pump, used to measures longest and shortest pump working time
    TickType_t time_pp_on_max;
    TickType_t time_pp_on_min;
}tDigIn_st;
static tDigIn_st dig_ins={
    .counter_in_states=0xff,
    .pump_power_in_states=0xff,
    .pump_on_acc=0,
    .time_pp_on_max=0,
    .time_pp_on_min=portMAX_DELAY,
};
//because it must be enough long time between flow-counter pulses 
//it is not required to protectect 'pump_last_run_time_ms' and 'press_val_at_cnt_pulse' by any interprocess sharing facilities 
//AND read/write 32bit value supposed to be atomic  
volatile uint32_t pump_last_run_time_ms=0; //pump working time sinse last flow-counter pulse, used for share
volatile float volume_at_WFpulse=0;
volatile TickType_t time_from_start_at_WFpulse=0;
volatile TickType_t time_pp_on_max;
volatile TickType_t time_pp_on_min;


static uint8_t relay_onoff_cmd=PP_REL_OFF;
static int32_t pump_is_on=0;

void DigInLoop(void* tmr) ;
static void RelaySwitchFSM(void);
float TankVolumeCalculation(int32_t pres);
static EventGroupHandle_t input_events;
//**********************************************************************************
void DigInInit(EventGroupHandle_t events){
    //pump relay control pin
    gpio_reset_pin(PUMP_RELAY_OUT_PIN);
    gpio_set_level(PUMP_RELAY_OUT_PIN, PP_REL_OFF);
    gpio_set_direction(PUMP_RELAY_OUT_PIN, GPIO_MODE_OUTPUT);
    gpio_set_level(PUMP_RELAY_OUT_PIN, PP_REL_OFF);
    gpio_reset_pin(PUMP_TRIAC_OUT_PIN);
    gpio_set_level(PUMP_TRIAC_OUT_PIN, 1);
    gpio_set_direction(PUMP_TRIAC_OUT_PIN, GPIO_MODE_OUTPUT);
    gpio_set_level(PUMP_TRIAC_OUT_PIN, 1);
    //inputs 
    gpio_config_t gpio_conf;
    gpio_conf.intr_type = GPIO_INTR_DISABLE;
    gpio_conf.mode = GPIO_MODE_INPUT;
    gpio_conf.pin_bit_mask = (1ULL<<COUNTER_IN_PIN) | (1ULL<<PUMP_POWER_IN_PIN) | (1ULL<<BYPASS_SW_POS_PIN);
    gpio_conf.pull_down_en = GPIO_PULLDOWN_DISABLE;
    gpio_conf.pull_up_en = GPIO_PULLUP_ENABLE;
    gpio_config(&gpio_conf);

    input_events=events;
    TimerHandle_t tmr=xTimerCreate("dig_in_tmr",pdMS_TO_TICKS(TIMER_GRANUL_MS),pdTRUE,NULL,DigInLoop);
    xTimerStart(tmr,0);
    dig_ins.pump_off_timer=0xffffffff;
}
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

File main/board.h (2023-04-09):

/* board.h - Board-specific hooks */

/*
 * Copyright (c) 2017 Intel Corporation
 * Additional Copyright (c) 2018 Espressif Systems (Shanghai) PTE LTD
 *
 * SPDX-License-Identifier: Apache-2.0
 */
#ifndef _BOARD_H_
#define _BOARD_H_

#include "driver/gpio.h"
#include "stdint.h"

#include "freertos/FreeRTOS.h"
#include "freertos/event_groups.h"
#include "freertos/task.h"

#define LED_ON  1
#define LED_OFF 0
#define PP_REL_ON  1
#define PP_REL_OFF 0

#define LED_B                   GPIO_NUM_2
#define BOARD_BUTTON_PIN        GPIO_NUM_0
#define COUNTER_IN_PIN          GPIO_NUM_17
#define PUMP_POWER_IN_PIN       GPIO_NUM_23
#define PUMP_RELAY_OUT_PIN      GPIO_NUM_4  //set to 1 for close contacts
#define PUMP_TRIAC_OUT_PIN      GPIO_NUM_16 //set to 0 for triac became conducting
#define BYPASS_SW_POS_PIN       GPIO_NUM_19
// #define I2C_MASTER_SCL_IO 26        /*!< gpio number for I2C master clock */
// #define I2C_MASTER_SDA_IO 25        /*!< gpio number for I2C master data  */

void LED_operation(uint8_t onoff);
void LED_toggle();
void PumpRelay(uint8_t onoff);
uint32_t IsPumpRun(void);

void board_init(void);

void DigInInit(EventGroupHandle_t events);
void DigInSetTankData(uint16_t vol,int32_t pres);
uint32_t IsBypassSwitchOn(void);
uint8_t IsButtonPressed(void);

#define MAX_PUMP_RUN_TIME_MNT   2
#define MAX_PUMP_RUN_TIME_MS   (MAX_PUMP_RUN_TIME_MNT*60*1000)
#define MIN_PUMP_STOPPED_TIME_SEC 10
#define MIN_PUMP_STOPPED_TIME_MS (MIN_PUMP_STOPPED_TIME_SEC*1000)

volatile extern uint32_t pump_last_run_time_ms;
volatile extern float volume_at_WFpulse;
volatile extern TickType_t time_from_start_at_WFpulse;
volatile extern TickType_t time_pp_on_max;
volatile extern TickType_t time_pp_on_min;

/* Pressure transmitter measuring range*/
#define PRES_TRANS_RANGE_bar  6.0   
#define ADC_REF_VOLT          2.048 //check adc PGA settings
#define ADC_MAX_CODE          0x7fff
//Input is differential signal between sensor 4-20mA voltage drop on Rshunt 
//and offset voltage. Ofset voltage tuned to be equal of voltage on Rshunt at 4mA sensor current.
//In this case we measure voltage drop on Rshunt concerned to current range 0-16mA
#define RSHUNT 130.0
#define PRES_ADC_MAX_CODE     ((0.016*RSHUNT*ADC_MAX_CODE)/ADC_REF_VOLT)

#define Pressure2ADCcode(pr)  (int32_t)(PRES_ADC_MAX_CODE*((pr)/PRES_TRANS_RANGE_bar))
#define ADCcode2Pressure(cd)  (PRES_TRANS_RANGE_bar*((float)(cd))/PRES_ADC_MAX_CODE)
#define ADC_1BAR (int32_t)(PRES_ADC_MAX_CODE*(1.0/PRES_TRANS_RANGE_bar))
#endif

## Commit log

2023-03-18 Added calculation of flow using pump head vs capacity data from datasheet
    [pressure model.xlsx]
2023-04-13 Added reception info from septic Output power (?) increased First 'total time' after power on is negative
2024-04-04 add system description
    [circuit.brd, circuit.sch]
